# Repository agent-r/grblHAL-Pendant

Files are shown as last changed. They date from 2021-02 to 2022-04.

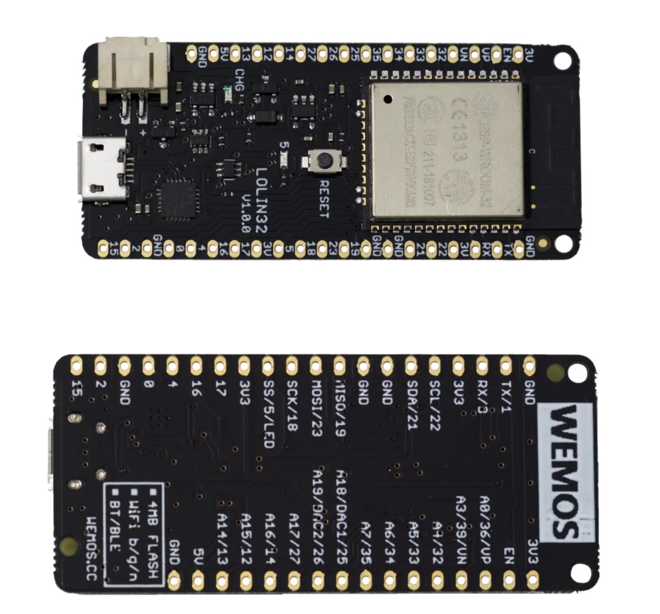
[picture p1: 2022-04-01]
Pictures/BoM/Lolin WeMos D32.jpg

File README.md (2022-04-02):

# grblHAL Pendant

(This project is working but still a bit work in progress)

I am using a WeMos Lolin32 microcontroller board to build a pendant for [grblHAL](https://github.com/grblHAL).

Machine state and position are passed from grblHAL via a plugin to a HC-05-Bluetooth-Module or a Esp01-Wifi-Module. The Pendant connects to one of these modules, receives this data and shows it on a tft display. 12 Buttons and a handwheel are there to send commands to the machine.

bCNC Pendant

## Basic functions:

- CNC pendant for up to 4 axis
- Rotary encoder and 12 buttons
- TFT display showing position and machine state
- Wireless connection (bluetooth or WiFi)
- Battery powered, charged via usb
- Control functions:
  - jogging (handwheel)
  - goto axis zero
  - set axis zero
  - Probing routine
  - Homing
  - Start
  - Stop/Hold
  - Unlock

## Bill of materials:

for the electronic parts see also [pictures here](/Pictures/BoM).

- grblHAL controller, breakout board is optional but recommended:
  - (https://github.com/grblHAL)
  - (https://github.com/phil-barrett/grblHAL-teensy-4.x)
  - (https://www.tindie.com/products/philba/grblhal-bob-unkit-for-teensy-41-t41u5xbb/)
- [Plugin for grblHAL](/grblHAL Plugin)
- Bluetooth (recommended) or WiFi module for the grblHAL side
- Pendant
  - WeMos Lolin32
  - 2.8" TFT Display
  - 12 Button KeyPad
  - Rotary encoder
  - LiPo Battery (to fit the case, it should be ??x??x??mm max)
  - Toggle Switch
  - PCB Board
  - 3d printed or milled case
  - Some screws (4pcs 2.2x6mm, 9pcs 2.2x16mm or similar)
  - Labels for keypad ([MISC folder](/MISC))
  - Micro USB cable for charging
  - [Firmware](/src) and some [libraries](/lib)

## HowTo: The grblHAL controller side

To be able to connect the pendant to grblHAL (at least if you use a Teensy4.1), you have to add a Bluetooth or Wifi module to your controller.

I recommend using WiFi (for example a ESP01 module), as I noticed some connection losses with bluetooth.

### Bluetooth:
The Module cannot be connected to the Teensy as it is. You have to program it first, by using AT-Commands. Instructions on how to do this can be found [all over the internet](https://www.google.com/search?q=how+to+program+a+hc+05+bluetooth+module+using+at+commands).

you sould:
- give your bluetooth module a proper name (for example "grblHAL")
- set the bluetooth module to "slave"
- set the bluetooth password to a 4-digit number
- set the bluetooth baudrate to "115200,0,0"
- read out the modules MAC address and write it down (you need it later)

### WiFi
The Wifi module cannot be connected to the Teensy as it is. You have to program it first.

- upload [this arduino application](/ESP-01 Webserver) to the module.
- Instructions on how to do this can be found [all over the internet](https://www.google.com/search?q=how+to+upload+an+arduino+sketch).
- once programmed via usb you can update the module also via OTA. Instructions on how to do this can be found [all over the internet](https://www.google.com/search?q=how+to+upload+an+arduino+sketch+OTA).

## How to: The pendant

- get all the parts from the Bill of materials
- **... to be continued ! ...**
- Close case using the 2.2x12mm screws

## How To: Getting started

- Start your grblHAL controller. A **Pendant** plugin should be named in your console window.
- check if your bluetooth or wifi network is available
- press **config** button and power cycle your pendant.
- navigate to **> Connection > Connection Mode** and select **Bluetooth** or **WiFi**
- navigate to **> Connection > Connection Settings**
    - if you are using wifi, set your SSID, Password, Host IP and port
    - if you are using bluetooth, set your Address and PIN (selecting slave by SSID does not work yet)
- check, if you want to change any other settings like jog speed, probing, sleep time, brightness, etc.
- leave the config menu and have fun!

## How to: Use

- Set your active axis by pressing one of the **Set** buttons
- Jog in active axis by turning **rotary knob** left/right
- Set current Position on active axis as WPOS zero by pressing **Set 0**
- Go to active axis zero by pressing **GoTo 0**
- Increase/decrease jogging distance by pressing **F+/F-**
- Start probing routine by pressing **Probe**
- **Start, stop, home or reset/unlock** by pressing the buttons (some have to be confirmed by pressing **Enter**)
- Change settings by pressing **Config**

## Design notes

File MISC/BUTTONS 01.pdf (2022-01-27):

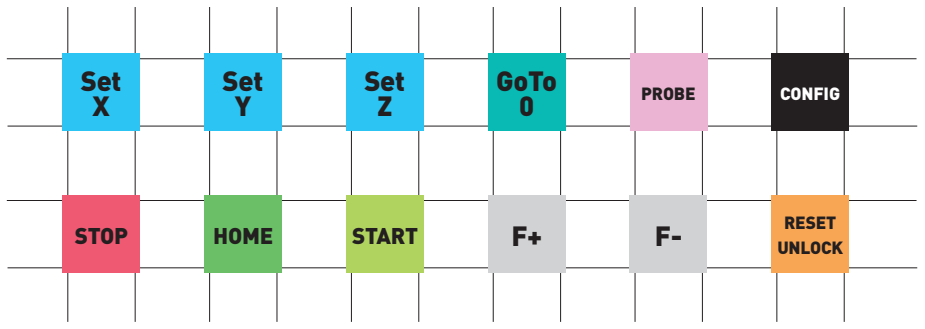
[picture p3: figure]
Set X; STOP; Set Y; HOME; Set Z; START; GoTo 0; PROBE; RESET UNLOCK F-; CONFIG

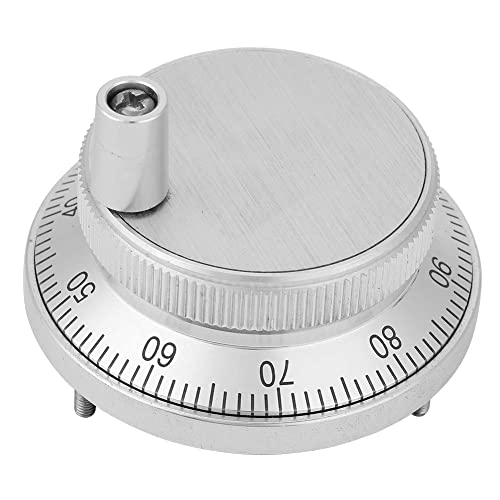
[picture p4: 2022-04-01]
Pictures/BoM/handwheel.jpg

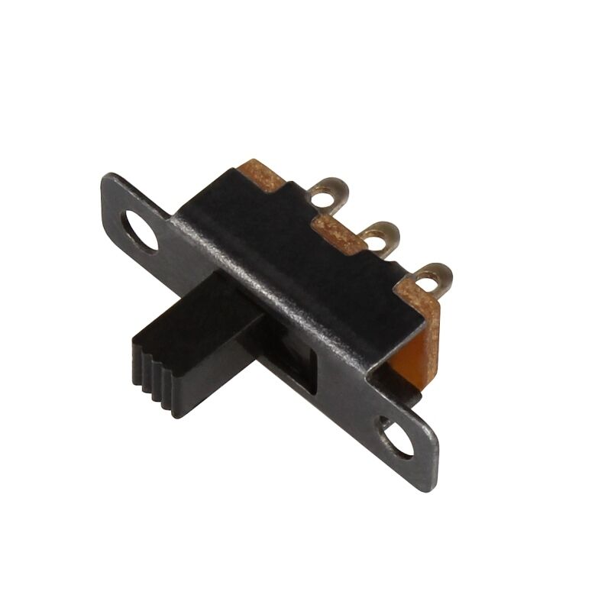
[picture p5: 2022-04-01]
Pictures/BoM/Switch.jpg

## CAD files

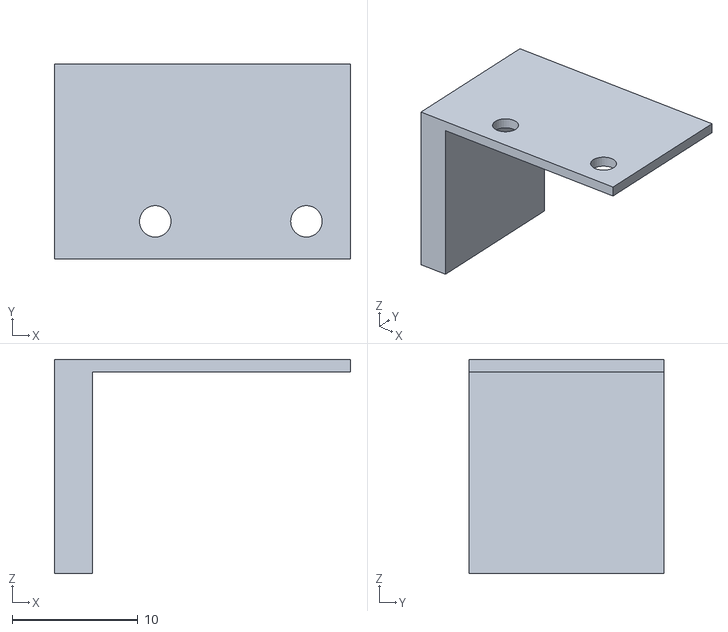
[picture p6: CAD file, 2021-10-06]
MISC/PENDANT 005 BOTTOM SWITCH ABDECKUNG.stl
23.5 x 15.5 x 17.0

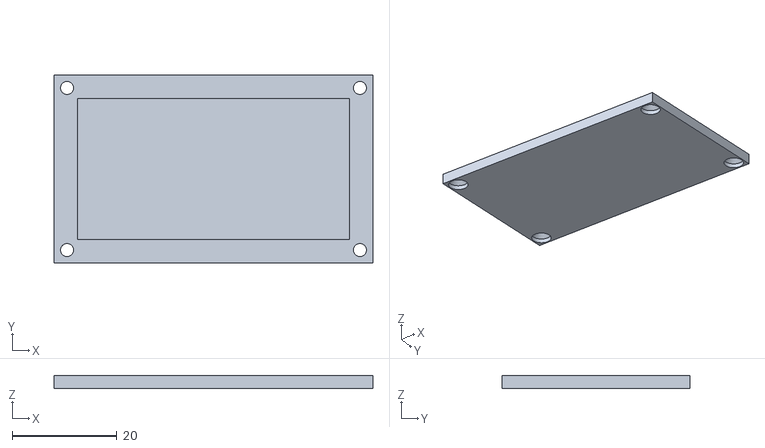
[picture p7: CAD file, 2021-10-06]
MISC/PENDANT 005 BOTTOM BATTERIEDECKEL.stl
61.0 x 36.0 x 2.50

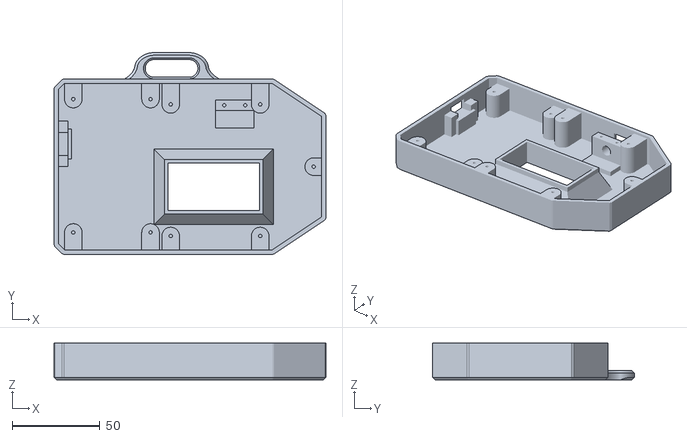
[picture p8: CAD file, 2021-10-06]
MISC/PENDANT 005 BOTTOM.stl
155.0 x 115.0 x 21.0

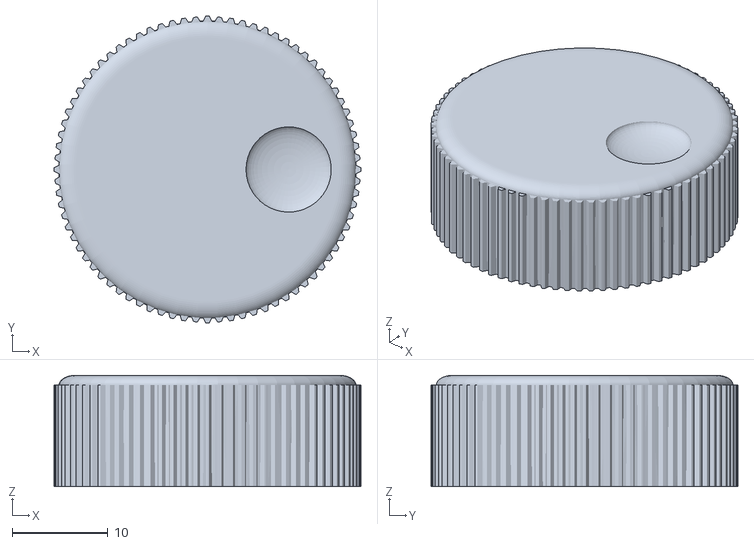
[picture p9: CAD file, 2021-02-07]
MISC/SPINNER KNOB 01.stl
32.0 x 32.0 x 11.6

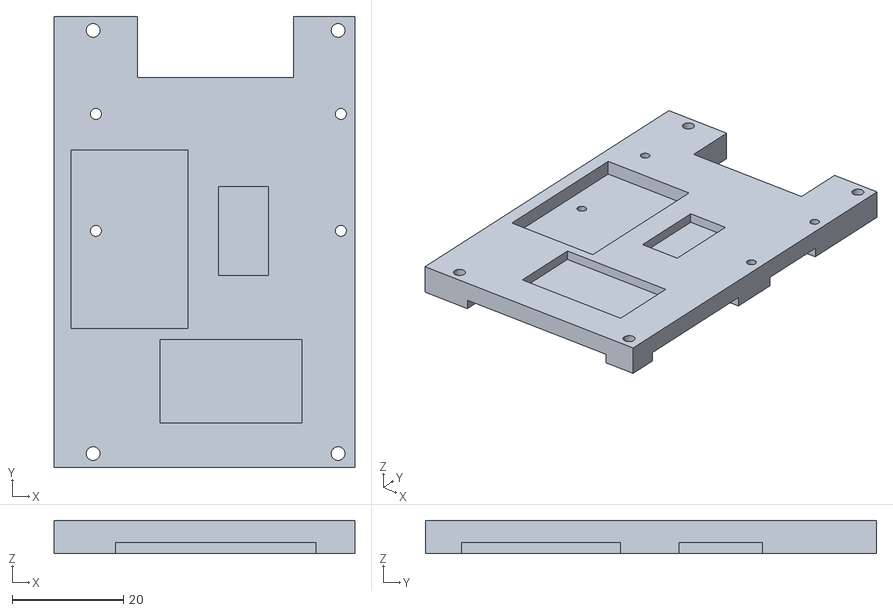
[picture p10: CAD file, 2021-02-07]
MISC/PENDANT 003 NODE MOUNT.stl
54.0 x 81.0 x 6.00

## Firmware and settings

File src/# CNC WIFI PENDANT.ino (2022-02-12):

/////////////////////////////////////////
//
//   GRBLHAL PENDANT
//
/////////////////////////////////////////

/////////////////////////////////////////
//
//   TODO:  -> Multi-Char Numbers in Config (BT Address, BT Pin, hosts) (sprintf ??)
//          ->
//
/////////////////////////////////////////


// PINS
////////////////////////////////////////
// 36   ROT CLK : A
// 39   ROT DT  : B
// 33   KEY SIG
// 21   TFT DC
// 18   TFT SCK
// --   TFT MISO
// 23   TFT MOSI
// 22   TFT CS
// 17   TFT LED
// VCC  TFT RESET
// 34   BATTERY VOLTAGE DIVIDER


// LIBRARIES
#include <WiFi.h>                   // WIFI
#include <WiFiClient.h>             // WIFI
#include "BluetoothSerial.h"
#include <EEPROM.h>                 // EEPROM
#include <TickTwo.h>                // TICKER
// #include "AiEsp32RotaryEncoder.h"   // ROTARY ENCODER
#include "ESP32Encoder.h"
#include <ArduinoJson.h>            // JSON
#include <SPI.h>                    // TFT
#include <TFT_eSPI.h>               // TFT
#include <analogWrite.h>            // TFT BRIGHTNESS
#include "fonts.h"                  // FONTS
#include "driver/adc.h"             // FOR SLEEP !
#include <esp_wifi.h>               // FOR SLEEP !
#include <esp_bt.h>                 // FOR SLEEP !


// DEBUG
static bool SERIAL_DEBUG = false;
static bool SERIAL_DEBUG_IN = false;


// WiFi & WiFi-AP
byte ConnectionMode = 0; // 0 = WIFI SLAVE    1 = WIFI AP    2 = BLUETOOTH SLAVE
WiFiClient TCPClient;

String WifiSSID;
String WifiPW;
IPAddress WifiHost(192,168,0,1);
int WifiPort = 8880;

String APSSID;
String APPW;
IPAddress APHost(192,168,0,1);
int APPort = 8880;

// BLUETOOTH
uint8_t BluetoothHost[6] = {0x00,0x21,0x13,0x01,0x3C,0x6F};
int BluetoothPin = 1234;
BluetoothSerial btSerial;
#if !defined(CONFIG_BT_ENABLED) || !defined(CONFIG_BLUEDROID_ENABLED)
#error Bluetooth is not enabled! Please run `make menuconfig` to and enable it
#endif


//EEPROM ADDRESSES
#define EEConnectionMode 0  //          Byte (1)
#define EEWifiSSID 1        // bis 30   String (30)
#define EEWifiPW 31         // bis 60   String (30)
#define EEWifiHost 61       // bis 64   IP (4)
#define EEWifiPort 65       // bis 66   Int (2)
#define EEAPSSID 67         // bis 96   String (30)
#define EEAPPW 97           // bis 126  String (30)
#define EEAPHost 127        // bis 130  IP (4)
#define EEAPPort 131        // bis 132  Int (2)
#define EEBluetoothHost 133 // bis 138  Adress (6)
#define EEBluetoothPin 139  // bis 140  Int (2)
#define EEJogSpeed 141      // bis 148  Int (4x2=8) XYZA
#define EEProbeOffset 149   // bis 152  Float (4)
#define EEProbeDepth 153    // bis 154  Int (2)
#define EEProbeSpeed 155    // bis 156  Int (2)
#define EEProbeBackHeight 157 //        Byte (1)
#define EEProbeTime 158     //          Byte (1)
#define EESleepTime 159     //          Byte (1)
#define EEBrightness 160    //          Byte (1)


// ROTARY ENCODER

#define ROTARY_ENCODER_A_PIN GPIO_NUM_36
#define ROTARY_ENCODER_B_PIN GPIO_NUM_39
/*
 #define ROTARY_ENCODER_BUTTON_PIN -1    // -1 if no Button
 #define ROTARY_ENCODER_VCC_PIN -1       // -1 if Vcc -> 3,3V
 #define ROTARY_ENCODER_STEPS 4
   volatile int rot_clicks = 0;
   AiEsp32RotaryEncoder rotaryEncoder = AiEsp32RotaryEncoder(ROTARY_ENCODER_A_PIN, ROTARY_ENCODER_B_PIN, ROTARY_ENCODER_BUTTON_PIN, ROTARY_ENCODER_VCC_PIN, ROTARY_ENCODER_STEPS);
   void IRAM_ATTR readEncoderISR() {
        rotaryEncoder.readEncoder_ISR();
   }
 */
ESP32Encoder rotaryEncoder;
#define ENCODER_FPS 5              // Update Rate for Sending Code
void checkEncoder();
TickTwo EncoderTicker(checkEncoder, (1000 / ENCODER_FPS));


// KEYPAD
#define KEYPAD_PIN GPIO_NUM_33       // ONLY ADC1-PINS !!!
#define KEYPAD_DEBOUNCE 80       // Debounce for Buttons
void checkKeypad();
TickTwo KeypadTicker(checkKeypad, (KEYPAD_DEBOUNCE));
int keypad_old;
int keypad_current;


// BATTERY CHECK
#define BATTERY_PIN GPIO_NUM_34
#define BATTERY_FACTOR 0.001736
#define BATTERY_LOW 3.35
#define BATTERY_HIGH 4.2
#define BATTERYCHECK 60    // Seconds
void checkBattery();
TickTwo BatteryTicker(checkBattery, (1000 * BATTERYCHECK));


// SLEEP
byte SleepTime = 1;     // Minutes till Sleep
void TFTSleep();
TickTwo SleepTicker(TFTSleep, (60000 * SleepTime)); // 60000
#define bitSet64(value, bit) ((value) |= (1ULL << (bit)))
uint64_t SleepPinMask = 0;

// TFT
// TFT PINS ARE DEFINED IN TFT_ESPI -> USER_SETUP.h
// #define TFT_SCK    18
// #define TFT_MOSI   23
// #define TFT_DC 21        //
// #define TFT_CS 22       //
// #define TFT_RST 4       // TO VCC !!!
#define TFT_LED GPIO_NUM_17
TFT_eSPI tft = TFT_eSPI();
#define TFT_FPS 20
void TFTUpdate();
TickTwo TftTicker(TFTUpdate, (1000 / TFT_FPS));

#define TFT_FONT_SMALL TFT_FONT_19
#define TFT_FONT_LARGE  TFT_FONT_28
#define TFT_COLOR_BGR 0xDEFB
#define TFT_COLOR_FRM_BGR 0xFFFF
#define TFT_COLOR_FRM_LIN 0x7BEF
#define TFT_COLOR_XYZ 0x0000
#define TFT_COLOR_XYZ_INACTIVE 0x94B2 // 0x8430
#define TFT_COLOR_STA_NRM 0x6680
#define TFT_COLOR_STA_ERR 0xF80A
#define TFT_COLOR_MSG_NRM 0x8430
#define TFT_COLOR_MSG_ERR 0xF80A
#define TFT_COLOR_CNF_STD 0x0000
#define TFT_COLOR_CNF_HIL 0xF80A
#define XField 0
#define YField 1
#define ZField 2
#define AField 3
#define FField 4
#define StateField 5
#define MessageField 6
#define tftRotation  2
byte TFT_BRIGHTNESS;

#define BLINK_FPS 3
void TFTBlink();
TickTwo BlinkTicker(TFTBlink, (1000 / BLINK_FPS));
bool blinker = true;
bool blinker_change = true;

#define MESSAGE 3       // Seconds to show Messages
void TFTMessage();
TickTwo MessageTicker(TFTMessage, (1000 * MESSAGE));

#define HOLD_TIME 2     // SECONDS from the last State. Or HOLD !!!
void Hold();
TickTwo HoldTicker(Hold, (1000 * HOLD_TIME));
bool hold = true;     // wait till connection is REALLY there !

//////////////////////////////////////////////////////////////////

uint16_t activeAxis = 0;
const String AxisName[4] = {"X", "Y", "Z", "A"};
const int AxisDir[4] = {1, 1, -1, 1};
int JogSpeed[4];
bool axischange = true;

float wx;
float wy;
float wz;
float wa;
float wxold;
float wyold;
float wzold;
float waold;
bool wxchange = true;
bool wychange = true;
bool wzchange = true;
bool wachange = true;

String state = "";
String stateold = "";
bool statechange = true;

byte activeFactor = 2;
const float factor[5] = {0.01, 0.1, 1, 10, 100};
const String strFactor[5] = {"0.01", "0.10", "1.00", "10.0", "100 "};
bool factorchange = true;


// PROBE
float ProbeOffset;     // Height of probe-button (mm/100) = 27.80mm
int ProbeSpeed;       // Speed to go down
int ProbeDepth;       // Distance to go down
byte ProbeBackHeight;  // Distance zo go up after probing
byte ProbeTime;        // Maximum Seconds to Wait for Probe Success / Failure
bool Probe_Alarm;   // flag to check Alarm

///////////////////////////////////////////////////////////////////////////
///////////////////////      SETUP       //////////////////////////////////
///////////////////////////////////////////////////////////////////////////

void setup() {

        Serial.begin(115200);
        pinMode(KEYPAD_PIN, INPUT);
        pinMode(BATTERY_PIN, INPUT);
        pinMode(TFT_LED, OUTPUT);

        // STARTING ENCODER INTERRUPTS:
        // rotaryEncoder.begin();
        // rotaryEncoder.setup(readEncoderISR);
        // rotaryEncoder.disableAcceleration();
        ESP32Encoder::useInternalWeakPullResistors=DOWN; // DOWN or UP?
        rotaryEncoder.attachSingleEdge(ROTARY_ENCODER_A_PIN, ROTARY_ENCODER_B_PIN);
        rotaryEncoder.setFilter(511);   // max 1023
        rotaryEncoder.setCount(0);

        tft.begin();
        tft.setRotation(tftRotation);

        if (SERIAL_DEBUG) {Serial.println("------- EEPROM START --------");}
        EEPROM.begin(512);

        ConnectionMode = EEPROM.read(EEConnectionMode);
        if (ConnectionMode == 0) { if (SERIAL_DEBUG) { Serial.println("ConnectionMode: WIFI SLAVE"); }}
        else if (ConnectionMode == 1) { if (SERIAL_DEBUG) { Serial.println("ConnectionMode: WIFI AP"); } }
        else if (ConnectionMode == 2) { if (SERIAL_DEBUG) { Serial.println("ConnectionMode: BLUETOOTH SLAVE"); } }

        WifiSSID = EepromReadString(EEWifiSSID, 30);
        if (SERIAL_DEBUG) { Serial.println("Wifi SSID: " + WifiSSID); }
        WifiPW = EepromReadString(EEWifiPW, 30);
        if (SERIAL_DEBUG) { Serial.println("Wifi PASSWORD: " + WifiPW); }
        WifiHost = EepromReadIP(EEWifiHost);
        if (SERIAL_DEBUG) { Serial.println ("Wifi HOST: " + String(WifiHost[0]) + "." + String(WifiHost[1]) + "." + String(WifiHost[2]) + "." + String(WifiHost[3]));}
        WifiPort = EepromReadInt(EEWifiPort);
        if (SERIAL_DEBUG) { Serial.println("Wifi PORT: " + String(WifiPort)); }

        APSSID = EepromReadString(EEAPSSID, 30);
        if (SERIAL_DEBUG) { Serial.println("AP SSID: " + APSSID); }
        APPW = EepromReadString(EEAPPW, 30);
        if (SERIAL_DEBUG) { Serial.println("AP PASSWORD: " + APPW); }
        APHost = EepromReadIP(EEAPHost);
        if (SERIAL_DEBUG) { Serial.println ("AP HOST: " + String(APHost[0]) + "." + String(APHost[1]) + "." + String(APHost[2]) + "." + String(APHost[3]));}
        APPort = EepromReadInt(EEAPPort);
        if (SERIAL_DEBUG) { Serial.println("AP PORT: " + String(APPort)); }

        BluetoothHost[0] = EEPROM.read(EEBluetoothHost); BluetoothHost[1] = EEPROM.read(EEBluetoothHost+1); BluetoothHost[2] = EEPROM.read(EEBluetoothHost+2); BluetoothHost[3] = EEPROM.read(EEBluetoothHost+3); BluetoothHost[4] = EEPROM.read(EEBluetoothHost+4); BluetoothHost[5] = EEPROM.read(EEBluetoothHost+5);
        if (SERIAL_DEBUG) { Serial.println("Bluetooth Host Address: " + String(BluetoothHost[0], HEX) + ":" + String(BluetoothHost[1], HEX) + ":" + String(BluetoothHost[2], HEX) + ":" + String(BluetoothHost[3], HEX) + ":" + String(BluetoothHost[4], HEX) + ":" + String(BluetoothHost[5], HEX)); }
        BluetoothPin = EepromReadInt(EEBluetoothPin);
        if (SERIAL_DEBUG) { Serial.println("Bluetooth Pin: " + String(BluetoothPin)); }

        JogSpeed[0] = EepromReadInt(EEJogSpeed);
        if (SERIAL_DEBUG) { Serial.println("X JOG SPEED: " + String(JogSpeed[0])); }
        JogSpeed[1] = EepromReadInt(EEJogSpeed+1);
        if (SERIAL_DEBUG) { Serial.println("Y JOG SPEED: " + String(JogSpeed[1])); }
        JogSpeed[2] = EepromReadInt(EEJogSpeed+2);
        if (SERIAL_DEBUG) { Serial.println("Z JOG SPEED: " + String(JogSpeed[2])); }
        JogSpeed[3] = EepromReadInt(EEJogSpeed+3);
        if (SERIAL_DEBUG) { Serial.println("A JOG SPEED: " + String(JogSpeed[3])); }

        ProbeOffset = EepromReadFloat(EEProbeOffset);
        if (SERIAL_DEBUG) { Serial.println("PROBE OFFSET: " + String(ProbeOffset)); }
        ProbeDepth = EepromReadInt(EEProbeDepth);
        if (ProbeDepth > 32767) { ProbeDepth = ProbeDepth - 65536; }
        if (SERIAL_DEBUG) { Serial.println("PROBE DEPTH: " + String(ProbeDepth)); }
        ProbeSpeed = EepromReadInt(EEProbeSpeed);
        if (SERIAL_DEBUG) { Serial.println("PROBE SPEED: " + String(ProbeSpeed)); }
        ProbeBackHeight = EEPROM.read(EEProbeBackHeight);
        if (SERIAL_DEBUG) { Serial.println("PROBE RISE: " + String(ProbeBackHeight)); }
        ProbeTime = EEPROM.read(EEProbeTime);
        if (SERIAL_DEBUG) { Serial.println("PROBE TIME: " + String(ProbeBackHeight)); }

        SleepTime = EEPROM.read(EESleepTime);
        SleepTicker.interval(SleepTime * 60000);
        if (SERIAL_DEBUG) { Serial.println("SLEEP TIME: " + String(SleepTime) + "min"); }

        TFT_BRIGHTNESS = EEPROM.read(EEBrightness);
        analogWrite(TFT_LED, TFT_BRIGHTNESS); // TURN LIGHT ON
        if (SERIAL_DEBUG) { Serial.println("BRIGHTNESS: " + String(TFT_BRIGHTNESS)); }

        if (SERIAL_DEBUG) {Serial.println("-------- EEPROM END ---------");}

        if (checkConfig()) { config(); } // Start config routine

        // STARTING INTERRUPTS !
        TftTicker.start();
        if (SleepTime > 0) { SleepTicker.start(); }
        KeypadTicker.start();
        EncoderTicker.start();
        BatteryTicker.start();
        // BlinkTicker.start();

        TFTPrepare();
        ConnectionSetup();
        Connect();

}

//////////////////////////////////////////////////////////////////



void loop() {
        TftTicker.update();
        EncoderTicker.update();
        KeypadTicker.update();
        BatteryTicker.update();
        // BlinkTicker.update();  // used only within config-loops
        MessageTicker.update();
        SleepTicker.update();
        HoldTicker.update();
}

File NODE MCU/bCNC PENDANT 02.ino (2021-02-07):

//
// D0  ROT CLK
// A0  KEY SIG
// D3  ROT DT
// D4  TFT DC
// D5  TFT SCK
// D6  TFT MISO
// D7  TFT MOSI
// D8  TFT CS
// 10  ROT SW !!

#include <ESP8266WiFi.h> // to turn off!

#include <Button2.h>
#include <REncoder.h>
#define ROTARY_PIN_CLK D0
#define ROTARY_PIN_DT D3
#define BUTTON_PIN 10
#define CLICKS_PER_STEP   4   // this number depends on your rotary encoder

REncoder rEncoder(ROTARY_PIN_CLK /* CLK Pin*/, ROTARY_PIN_DT /* DT Pin */, BUTTON_PIN /* SW Pin */);
int RPos = 0;

// ESPRotary r = ESPRotary(ROTARY_PIN_CLK, ROTARY_PIN_DT, CLICKS_PER_STEP);
// Button2 b = Button2(BUTTON_PIN);

#define KEYPAD_PIN A0

#include <ArduinoJson.h>

StaticJsonDocument<128> JsonIn;
StaticJsonDocument<64> JsonOut;

int lasttouched = 0;
int currtouched = 0;

#include <Ticker.h>
void TFTUpdate();
Ticker TFTTicker(TFTUpdate, 200);

#include <SPI.h>
#include <Adafruit_GFX.h>
#include <Adafruit_ILI9341.h>
#include <Adafruit_I2CDevice.h>
#define TFT_DC D4
#define TFT_CS D8
Adafruit_ILI9341 tft = Adafruit_ILI9341(TFT_CS, TFT_DC);
int tftRotation = 0;


/////////////////////////////////////////////////////////////////

uint16_t activeAxis = 0;
String AxisName[4] = {"", "X", "Y", "Z"};

float wx = 1;
float wy = 1;
float wz = 1;
String state = "";
float wxold = 1;
float wyold = 1;
float wzold = 1;
String stateold = "";
bool wxchange = true;
bool wychange = true;
bool wzchange = true;
bool statechange = true;
bool factorchange = true;
bool axischange = true;
uint16_t activeFactor = 2;
float factor[5] = {0.01, 0.1, 1, 10, 100};
String strFactor[5] = {"0.01", "0.10", "1.00", "10.0", "100 "};
String LastSentCommand = "";
String StatusMessage = "";
int StatusMessageCounter = 0;
int MessageTime = 15;

/////////////////////////////////////////////////////////////////


//////////////////////////////////////////////////////////////////

void setup() {

    WiFi.mode( WIFI_OFF );
    WiFi.forceSleepBegin();

    Serial.setTimeout(50); // 200 works good - less ???
    Serial.begin(128000);
    while (!Serial) { // needed to keep leonardo/micro from starting too fast!
        delay(50);
    }


    // rEncoder.setMinEncoderPosition(-1);
    // rEncoder.setMaxEncoderPosition(1);
    // r.setChangedHandler(rotate);
    // b.setTapHandler(click);

    // stateTicker.start();
    TFTTicker.start();

    tft.begin();
    tft.setRotation(tftRotation);
    tft.fillScreen(ILI9341_BLACK);
    tft.setCursor(0, 00);
    tft.setTextColor(ILI9341_YELLOW); tft.setTextSize(2);

    tft.println("Starting Pendant ...");
    tft.println("");

    delay(500); // ????

    tft.fillRect(0, 0, 240, 320, ILI9341_BLACK);
}


void loop() {

    getRotary();
    getButton();
    getState();

    TFTTicker.update();
}


///////////////////////// ROT ENCODER ////////////////////////////////////////

void getRotary() {
    // REncoder::Event encoderEvent = rEncoder.reState();

    switch (rEncoder.reState()) {
    case REncoder::Event::REncoder_Event_Rotate_CW:
        if( digitalRead(ROTARY_PIN_CLK) == HIGH) {
            if (activeAxis != 0) {
                sendCmd("G", "G91G0" + AxisName[activeAxis] + (factor[activeFactor] * (-1 * rEncoder.getPosition())));
                sendCmd("G", "G90");
            }
            else {PrintStatus("ERROR: No Axis!", ILI9341_WHITE);}
        }
        rEncoder.setPosition(0);
        break;
    case REncoder::Event::REncoder_Event_Rotate_CCW:
        if( digitalRead(ROTARY_PIN_CLK) == HIGH) {
            if (activeAxis != 0) {
                sendCmd("G", "G91G0" + AxisName[activeAxis] + (factor[activeFactor] * (-1 * rEncoder.getPosition())));
                sendCmd("G", "G90");
            }
            else {PrintStatus("ERROR: No Axis!", ILI9341_WHITE);}
        }
        rEncoder.setPosition(0);
        break;
    case REncoder::Event::REncoder_Event_Switch_Pushed:
        if (activeAxis != 0) {
            sendCmd("G", "G10L20P1" + AxisName[activeAxis] + "0");
        }
        else { PrintStatus("ERROR: No Axis!", ILI9341_WHITE); }
        break;
    case REncoder::Event::REncoder_Event_None:
        break;
    }

}



/////////////////////////////////////////////////////////////////

void getButton() {

    currtouched = readButton();
    delay(10);
    if (currtouched != readButton()) {return;}

    if (currtouched != lasttouched) {
        switch (currtouched) {
        case -1:
            break;
        case 0:
            setX();
            break;
        case 1:
            setY();
            break;
        case 2:
            setZ();
            break;
        case 3:
            homeX();
            break;
        case 4:
            homeY();
            break;
        case 5:
            homeZ();
            break;
        case 6:
            decreaseFactor();
            break;
        case 7:
            increaseFactor();
            break;
        case 8:
            homeAll();
            break;
        case 9:
            run();
            break;
        case 10:
            stop();
            break;
        case 11:
            reset_unlock();
            break;
        default:
            // Statement(s)
            break;
        }
    }
    lasttouched = currtouched;
}

int readButton() {
    int analogValue = analogRead(KEYPAD_PIN);
    if (analogValue < 450) {
        return(-1);
    } else if (analogValue < 520) {
        return(0);
    } else if (analogValue < 540) {
        return(1);
    } else if (analogValue < 570) {
        return(2);
    } else if (analogValue < 600) {
        return(3);
    } else if (analogValue < 650) {
        return(4);
    } else if (analogValue < 700) {
        return(5);
    } else if (analogValue < 750) {
        return(6);
    } else if (analogValue < 800) {
        return(7);
    } else if (analogValue < 850) {
        return(8);
    } else if (analogValue < 930) {
        return(9);
    } else if (analogValue < 1000) {
        return(10);
    } else {
        return(11);
    }
}


////////////////////////

void getState() {

    if (Serial.available() > 0) {
        deserializeJson(JsonIn, Serial);
        wz = JsonIn["wz"]; // 0.1
        wy = JsonIn["wy"]; // 0.1
        wx = JsonIn["wx"]; // 0.1
        const char* statechar = JsonIn["state"];
        state = String(statechar);
        if (wx != wxold) { wxchange = true; wxold = wx; }
        if (wy != wyold) { wychange = true; wyold = wy; }
        if (wz != wzold) { wzchange = true; wzold = wz; }
        if (state != stateold) { statechange = true; stateold = state; }
    }

}

void sendCmd(String type, String cmd) {
    JsonOut.clear();
    JsonOut[type] = cmd;
    serializeJson(JsonOut, Serial);
    Serial.print(";");

    if ((cmd == "G90") || (cmd == "UNLOCK")) {
        LastSentCommand = LastSentCommand + " " + cmd;
    }
    else {
        LastSentCommand = cmd;
    }
    PrintStatus(LastSentCommand, ILI9341_WHITE);
}
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

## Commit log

2021-02-07 First Version
    [PENDANT 003 BOTTOM.stl, PENDANT 003 NODE MOUNT.stl, PENDANT 003 TOP.stl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]
2022-01-27 Work in Progress
    [PENDANT CABLE CONNECTIONS.ods]
